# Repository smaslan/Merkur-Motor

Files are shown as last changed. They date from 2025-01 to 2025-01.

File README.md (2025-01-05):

# Stepper Motor Controller

This is simple project of one stepper motor controller designed for Czech toy 
[Merkur](https://www.merkurtoys.cz). It has manual speed and direction controlls and Bluetooth module for remote control via terminal commands or Android app. 
I don't expect this project as a whole would be useful to most people
but it may serve as a source for canibalization of some of its parts.

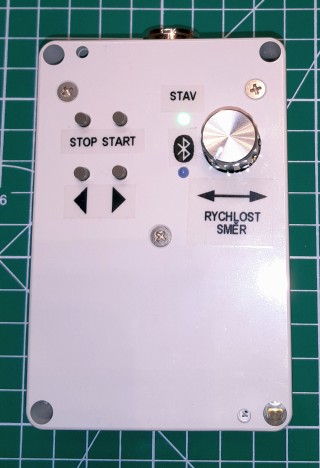
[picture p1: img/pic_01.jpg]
Controller box

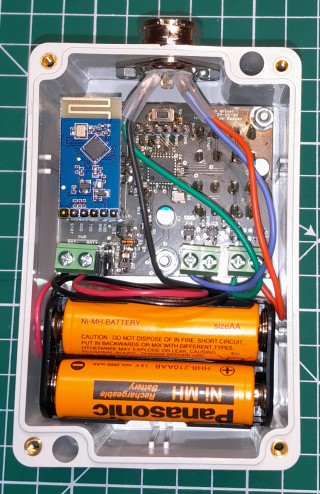
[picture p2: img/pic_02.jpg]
Controller insides


## Hardware

It was designed in a hurry from parts I had on hand so it's far from being optimal.
Core of the controller is 8-bit AVR [ATmega328PB](https://www.microchip.com/en-us/product/atmega328pb) (ATmega168PB would be enough). 
I used stepper motor [NEMA 17HS4023](https://www.google.com/search?q=NEMA+17+17HS4023) with bipolar coils.
I did not have proper stepper controller IC on hand, so I used cheap GaN fet driver ICs 
[1EDN7512B](https://www.infineon.com/cms/en/product/power/gate-driver-ics/1edn7512b/) with MOSFET half-bridge output.
These chips have undervoltage lockout (UVLO) circuit with threshold around 4.2V, which is kind of risky, because one of the bridge ICs will go to 
UVLO state before the other one, so there may be uninteruptable current via the winding when UVLO goes active. It won't be destructive, but it will discharge battery even faster, 
so UVLO is detected by AVR and it turns off power stage before it happens. Remote communication is made using cheap BT module
[JDY33-TTL](https://www.google.com/search?q=jdy33+ssp). Power stage, BT module and voltage sensing circuit can be switched off 
by power MOSFET to reduce idle power consumption to near zero (approx 2uA). Intended supply is from 4xAA NiMH accumulators, so there is 
5V voltage regulator for AVR. I used ultra-low quiscent current LDO TI [TPS709B50](https://www.ti.com/product/TPS709). 
Controlls are four buttons (Start, Stop, Left, Right) and encoder to setup speed.

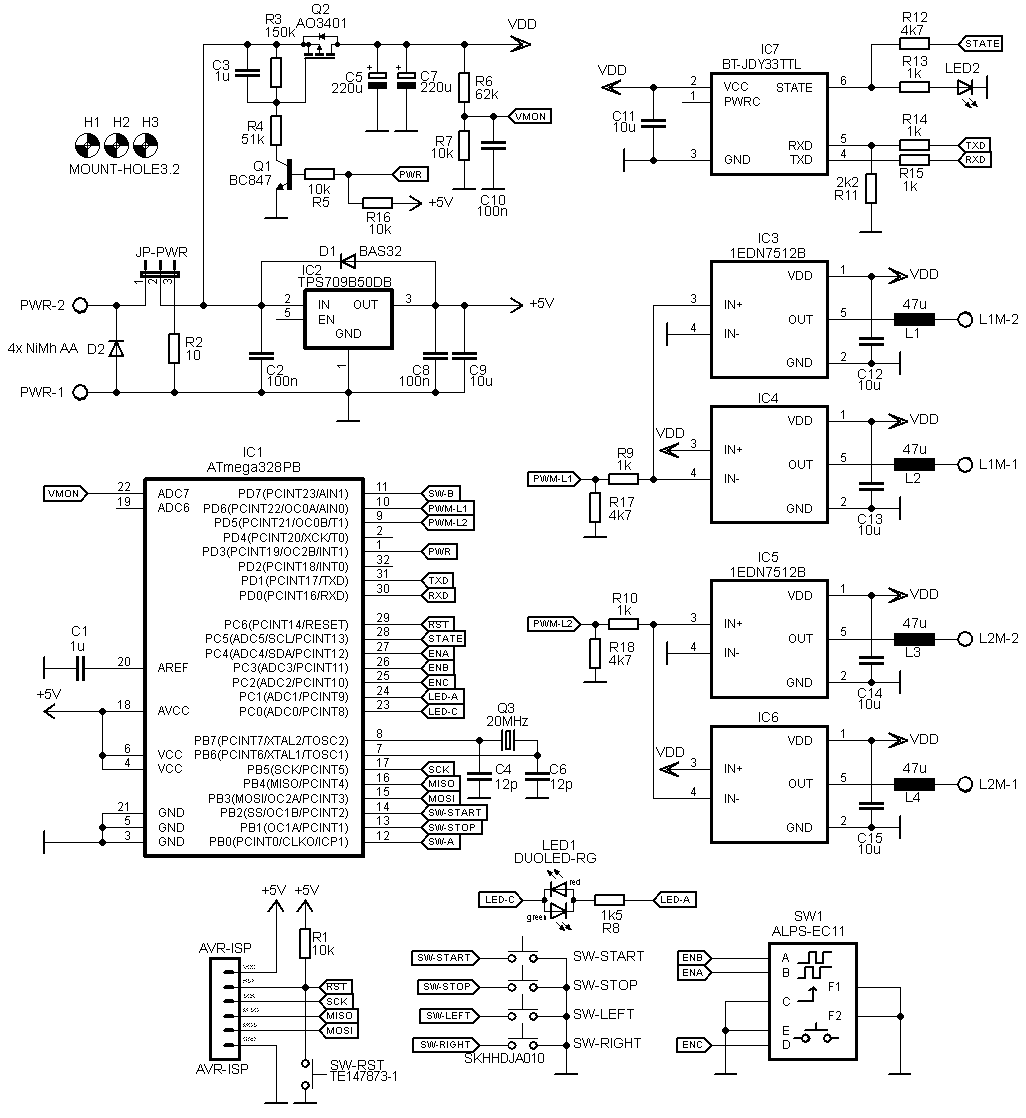
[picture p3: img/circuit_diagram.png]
Circuit diagram


The whole module was designed to fit in [plastic box](https://www.tme.eu/cz/details/km-276i_g/univerzalni-krabicky/maszczyk/). I wanted to make it smaller, but batteries are a bit large. Maybe in the next version. [PCB and diagram](./stepper_ctrl/) are available in Eagle format.

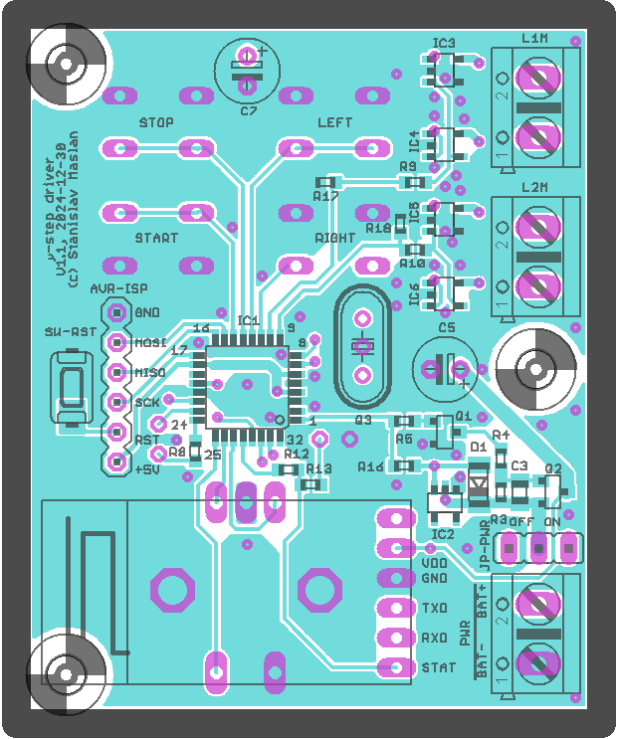
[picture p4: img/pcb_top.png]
PCB top layer

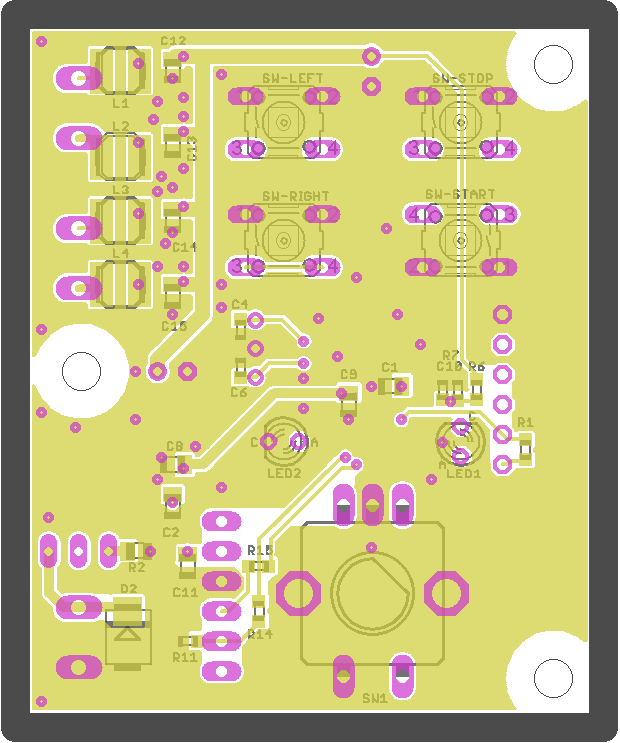
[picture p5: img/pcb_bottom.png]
PCB bottom layer


## AVR Firmware

Firmware for AVR is written in [Microchip Studio](https://www.microchip.com/en-us/tools-resources/develop/microchip-studio) using AVRGCC. 
Motor bridges are controlled by AVR PWM outputs which generate sine and cosine waves with modulation frequency of 78.125kHz, so it is kind of micro stepping driver. 
There is no current feedback from the stepper windings, so the current is controlled empirically by changing sine and consine amplitudes depending on motor speed. For the selected motor it should be approx 200 - 250mA with no load. Maximum speed is limited to 270rpm.
Reception of data via BT module is made in ISR to round buffer. Processing of the commands is done in main loop as well as controls state machine and other non-critical operations. Command interface uses simple [SCPI command](https://en.wikipedia.org/wiki/Standard_Commands_for_Programmable_Instruments) style commands set. Each command must be terminated by LF. Commands can be chained by semicolon. Answers are terminated by LF. Communication runs on BT module's default 9600bd. BT device name and its MAC address was left on default. List of supported commands:

```
 *IDN?                   - Return identification string.
 *OPC?                   - Wait for previous commands being processed, then returns 1.
 SYST:ERR?               - Return last error string.
 SYST:VMON?              - Return system voltage [V].
 SYST:TEMP?              - Return system temperature [degC].
 SYST:EESAVE             - Store current setup to EEPROM.
 SLEEP                   - Go to sleep mode immediately.
 SLEEP:TIMEOUT <timeout> - set sleep mode timeout [s].
 SLEEP:TIMEOUT?          - Get sleep timeout [s].
 SPEED <speed>           - Set motor speed in [rpm], signed value to set direction.
 SPEED?                  - Get current motor speed [rpm].
 SPEED:SET?              - Get last target (set) speed [rpm].
 SPEED:LIMIT <speed>     - Set speed limit [rpm].
 SPEED:LIMIT?            - Get speed limit [rpm].
 MOT:ACC <acc>           - Set motor acceleration constant [rpm/s].
 MOT:ACC?                - Get motor acceleration constant [rpm/s].
 START                   - Start motor to last set speed and direcion.
 STOP                    - Stop motor.
 DIR <direction>         - set motor direction (CW or CCW) 
                           and eventually start motor to previous speed.
```

Controller has implemented timeout timer, so when no controls are changed or SCPI command received, it will go to power down mode. It will respond to START button press to wakeup. It can be forced to power down mode by holding STOP button or by SCPI command SLEEP. Battery voltage is measured continuously. When it drops below preset threshold it will start blinking red and eventually turn off.

AVR fuse bits:
```
 Extended byte: CFD = 0, BODLEVEL[2..0] = 101 
 High byte: BOOTRST = 1, BOOTSZ[1..0] = 00, EESAVE = 0, WDTON = 1, SPIEN = 0, DWEN = 0, RSTDISBL = 1
 Low byte: CKSEL[3..0] = 1111, SUT[1..0] = 11, CKOUT = 1, CKDIV8 = 1
```

Firmware is available at [stepper_ctrl/fw_stepper_v1/](./stepper_ctrl/fw_stepper_v1).

## Android controll app "Merkur Motor"

Stepper controller can be controlled by terminal, but it's not exactly practical, so I decided to make an app for Android. This was my first atempt ever, so be warned it is not nice and optimal code but may be still used to cannibalize some parts. 
After some reading I decided to give a try to [Android Studio](https://developer.android.com/studio) and popular language [Kotlin](https://kotlinlang.org). That turned out to be good choice. Especially Kotlin is nice and simple language compared to e.g. C++. 
At first I tried to use some BT serial libraries, but I was not able to deal with collisions between some libraries so I tried to make BT communication using basic libraries. That was simpler than expected. Basically just list paired BT devices, select one, open BT socket and get in/out streams. Done. The worst part was dealing with permissions and trying to deal with loss of communication e.g. when the BT device goes offline. But in the end it kind of works at least from Android 11 to 14. Source is available at [MerkurControl/](./MerkurControl/).

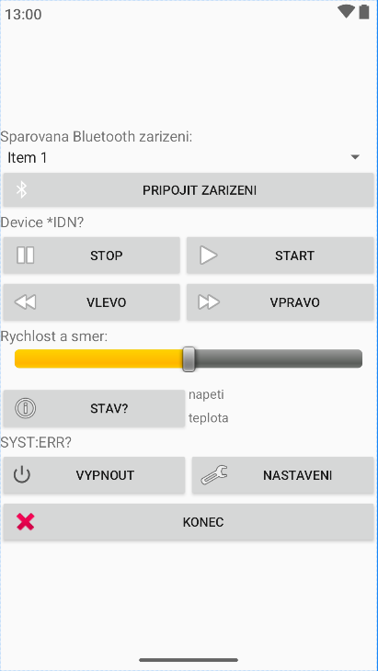
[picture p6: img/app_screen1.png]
Android app


## License
All parts of the project are distributed under [MIT license](./README.txt).

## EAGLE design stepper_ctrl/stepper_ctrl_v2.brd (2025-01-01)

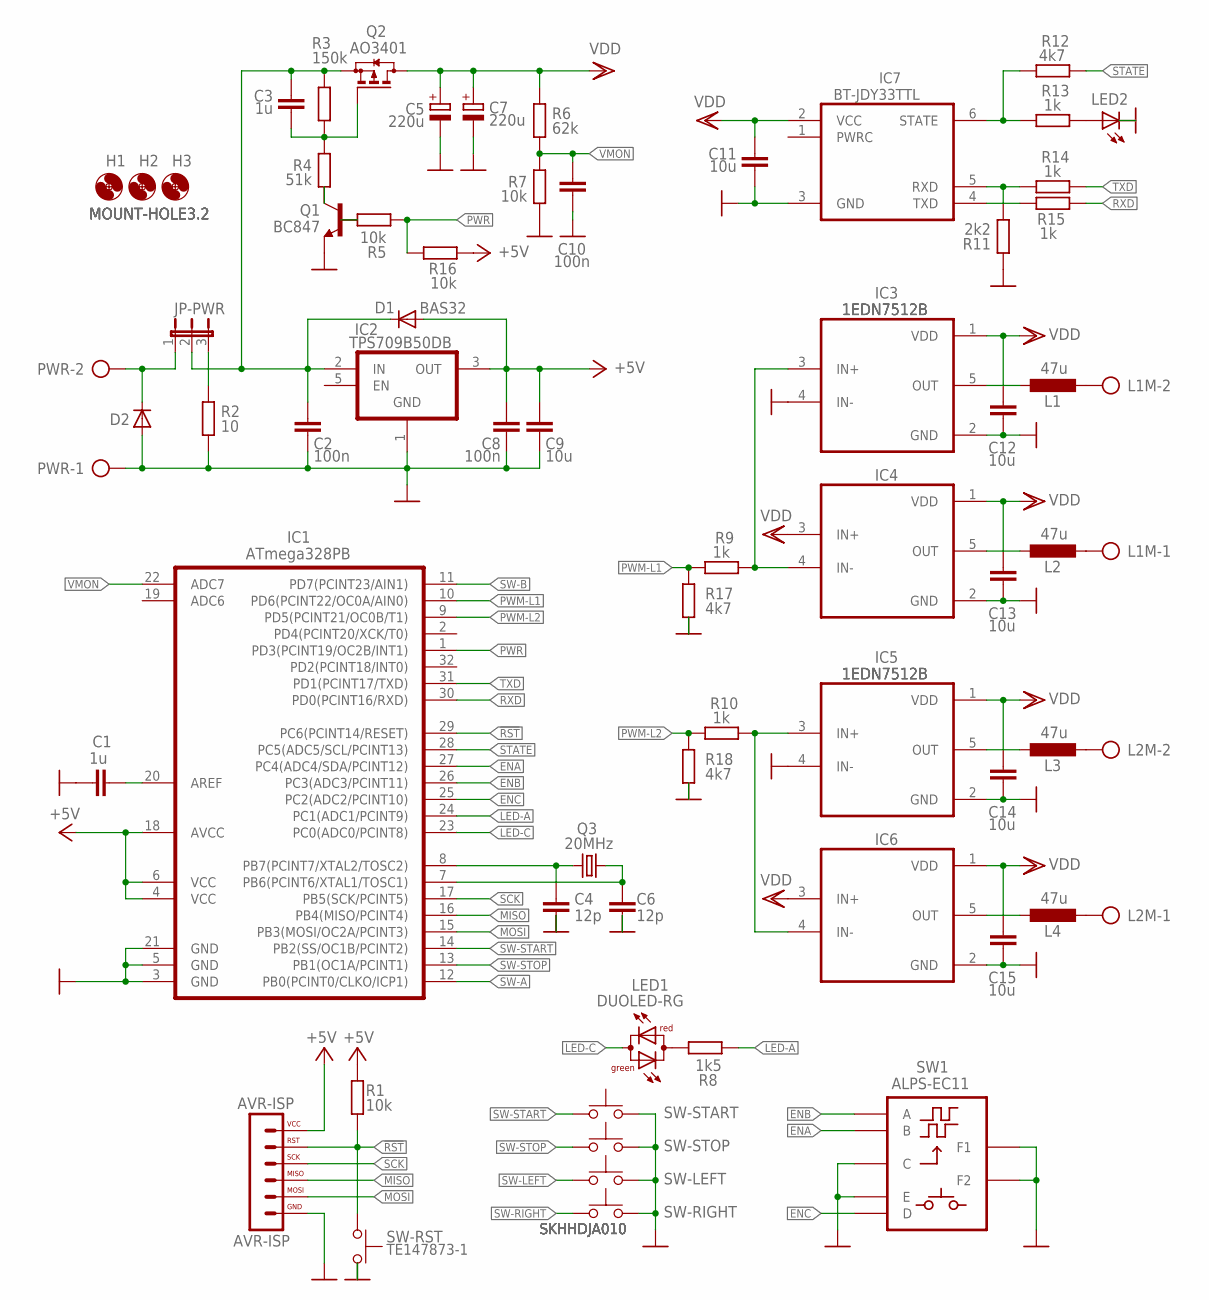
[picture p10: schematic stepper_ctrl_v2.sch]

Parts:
AVR-ISP: AVR-ISP; SIL6-NNRND
C1, C3: 1u; C0805K
C2, C8: 100n; C0805K
C4, C6: 12p; C0603K
C5, C7: 220u; E2,5-6
C9, C11, C12, C13, C14, C15: 10u; C0805K
C10: 100n; C0603K
D1: BAS32; SOD80C
D2: DIODE-SMB; SMB
H1, H2, H3: MOUNT-HOLE3.2; 3,2
IC1: ATmega328PB; TQFP32
IC2: TPS709B50DB; SOT23-5
IC3, IC4, IC5, IC6: 1EDN7512B; SOT23-5
IC7: BT-JDY33TTL; BT-JFY33TTL
JP-PWR: JP2EB; JP2YB
L1, L2, L3, L4: 47u; L4018
L1M, L2M: AK500/2
LED1: DUOLED-RG; LED3MM
LED2: LED3MM
PWR: AK500/2
Q1: BC847; SOT23
Q2: AO3401; SOT23
Q3: 20MHz; HC49U-V
R1, R5, R7, R16: 10k; R0603
R2: 10; R0805
R3: 150k; R0603
R4: 51k; R0603
R6: 62k; R0603
R8: 1k5; R0603
R9, R10, R13, R14, R15: 1k; R0603
R11: 2k2; R0603
R12, R17, R18: 4k7; R0603
SW1: ALPS-EC11; ALPS_EC11
SW-LEFT: SKHHDJA010; CUDL1
SW-RIGHT: SKHHDJA010; CUDL1
SW-RST: TE147873-1; TE-147873-1
SW-START: SKHHDJA010; CUDL1
SW-STOP: SKHHDJA010; CUDL1

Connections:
!RST: AVR-ISP.5, IC1.29 (PC6(PCINT14/RESET)), R1.2, SW-RST.P$2
+5V: AVR-ISP.6, C8.1, C9.1, D1.A, IC1.4 (VCC), IC1.6 (VCC), IC1.18 (AVCC), IC2.3 (OUT), R1.1, R16.2
ENA: IC1.27 (PC4(ADC4/SDA/PCINT12)), SW1.B
ENB: IC1.26 (PC3(ADC3/PCINT11)), SW1.A
ENC: IC1.25 (PC2(ADC2/PCINT10)), SW1.D
GND: AVR-ISP.1, C1.1, C2.2, C4.2, C5.-, C6.2, C7.-, C8.2, C9.2, C10.2, C11.2, C12.2, C13.2, C14.2, C15.2, D2.A, IC1.3 (GND), IC1.5 (GND), IC1.21 (GND), IC2.1 (GND), IC3.2 (GND), IC3.4 (IN-), IC4.2 (GND), IC5.2 (GND), IC5.4 (IN-), IC6.2 (GND), IC7.3 (GND), LED2.K (C), PWR.1, Q1.2 (E), R2.1, R7.1, R11.2, R17.2, R18.2, SW1.C, SW1.E, SW1.F1, SW1.F2, SW-LEFT.1, SW-LEFT.2, SW-RIGHT.1, SW-RIGHT.2, SW-RST.P$1, SW-START.1, SW-START.2, SW-STOP.1, SW-STOP.2
LED-A: IC1.24 (PC1(ADC1/PCINT9)), R8.1
LED-C: IC1.23 (PC0(ADC0/PCINT8)), LED1.K (C)
MISO: AVR-ISP.3, IC1.16 (PB4(MISO/PCINT4))
MOSI: AVR-ISP.2, IC1.15 (PB3(MOSI/OC2A/PCINT3))
unnamed: IC3.3 (IN+), IC4.4 (IN-), R9.1
unnamed: C1.2, IC1.20 (AREF)
unnamed: C2.1, C3.1, D1.C, IC2.2 (IN), JP-PWR.2, Q2.2 (S), R3.1
unnamed: D2.C, JP-PWR.1, PWR.2
unnamed: IC5.3 (IN+), IC6.4 (IN-), R10.1
unnamed: JP-PWR.3, R2.2
unnamed: LED2.A, R13.1
unnamed: IC7.6 (STATE), R12.2, R13.2
unnamed: IC7.5 (RXD), R11.1, R14.2
unnamed: IC7.4 (TXD), R15.2
unnamed: C4.1, IC1.8 (PB7(PCINT7/XTAL2/TOSC2)), Q3.1
unnamed: C6.1, IC1.7 (PB6(PCINT6/XTAL1/TOSC1)), Q3.2
unnamed: Q1.1 (B), R5.2
unnamed: LED1.A, R8.2
unnamed: IC3.5 (OUT), L1.2
unnamed: IC4.5 (OUT), L2.2
unnamed: IC5.5 (OUT), L3.2
unnamed: IC6.5 (OUT), L4.2
unnamed: L1.1, L1M.2
unnamed: L2M.2, L3.1
unnamed: L2M.1, L4.1
unnamed: L1M.1, L2.1
unnamed: C3.2, Q2.1 (G), R3.2, R4.2
unnamed: Q1.3 (C), R4.1
PWM-L1: IC1.10 (PD6(PCINT22/OC0A/AIN0)), R9.2, R17.1
PWM-L2: IC1.9 (PD5(PCINT21/OC0B/T1)), R10.2, R18.1
PWR: IC1.1 (PD3(PCINT19/OC2B/INT1)), R5.1, R16.1
RXD: IC1.30 (PD0(PCINT16/RXD)), R15.1
SCK: AVR-ISP.4, IC1.17 (PB5(SCK/PCINT5))
STATE: IC1.28 (PC5(ADC5/SCL/PCINT13)), R12.1
SW-A: IC1.12 (PB0(PCINT0/CLKO/ICP1))
SW-B: IC1.11 (PD7(PCINT23/AIN1))
SW-LEFT: SW-LEFT.3, SW-LEFT.4
SW-RIGHT: SW-RIGHT.3, SW-RIGHT.4
SW-START: IC1.14 (PB2(SS/OC1B/PCINT2)), SW-START.3, SW-START.4
SW-STOP: IC1.13 (PB1(OC1A/PCINT1)), SW-STOP.3, SW-STOP.4
TXD: IC1.31 (PD1(PCINT17/TXD)), R14.1
VDD: C5.+, C7.+, C11.1, C12.1, C13.1, C14.1, C15.1, IC3.1 (VDD), IC4.1 (VDD), IC4.3 (IN+), IC5.1 (VDD), IC6.1 (VDD), IC6.3 (IN+), IC7.2 (VCC), Q2.3 (D), R6.2
VMON: C10.1, IC1.22 (ADC7), R6.1, R7.2

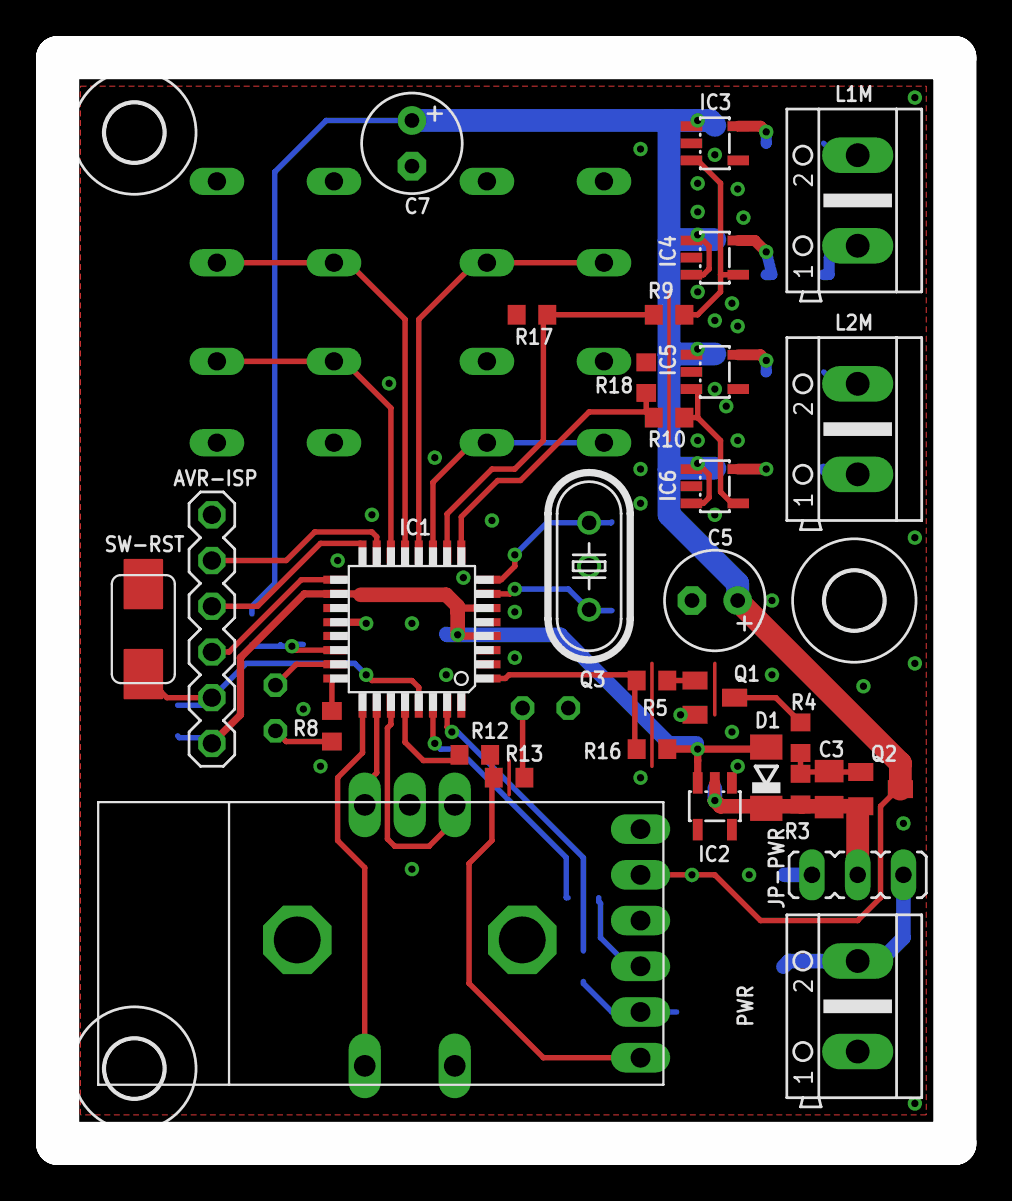
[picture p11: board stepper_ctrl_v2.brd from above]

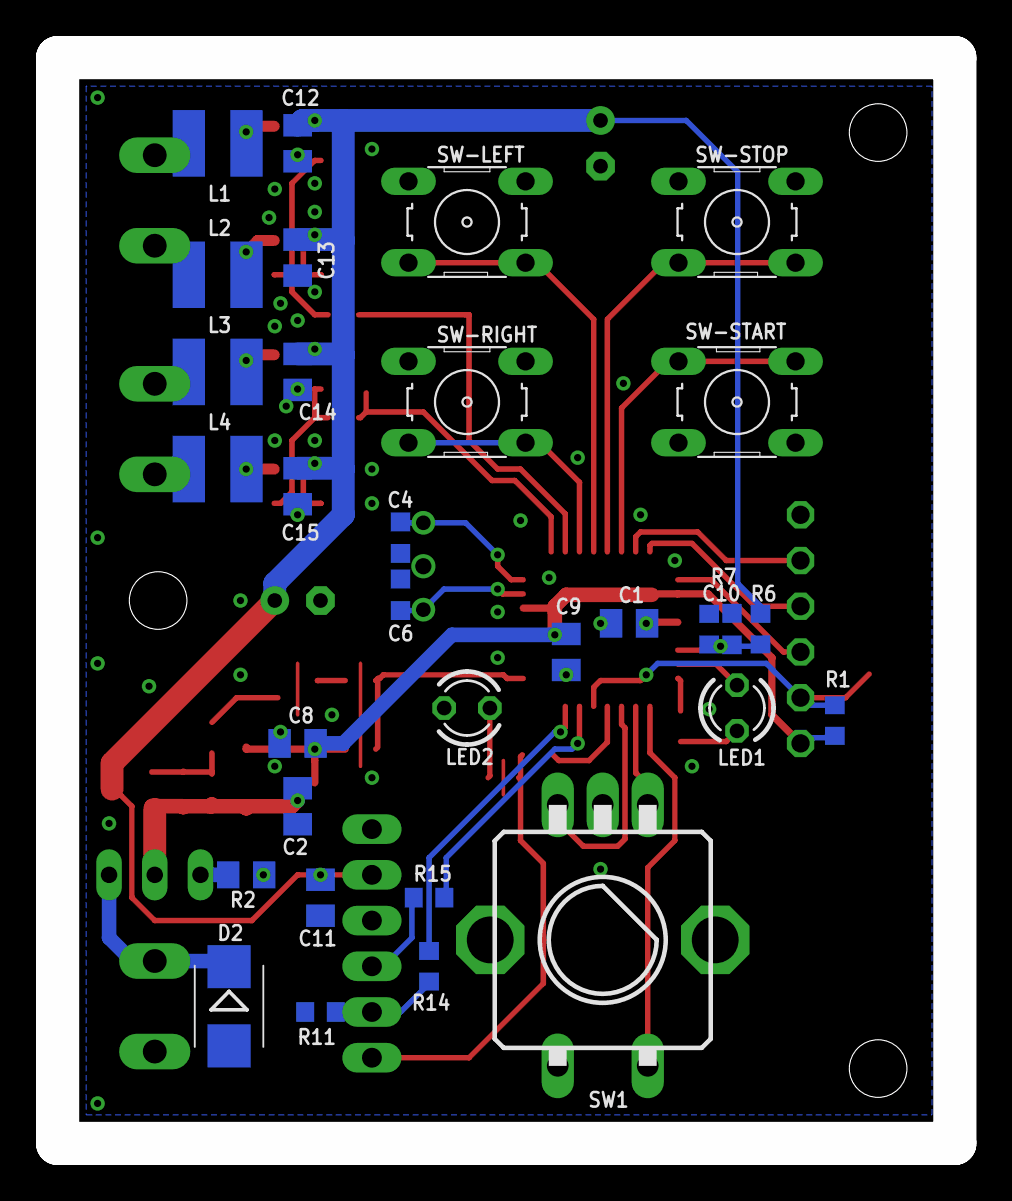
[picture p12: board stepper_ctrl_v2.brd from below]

Board: 2 copper layers, 49.8 x 60.3 mm, 65 parts (31 on the bottom side), 47 nets.

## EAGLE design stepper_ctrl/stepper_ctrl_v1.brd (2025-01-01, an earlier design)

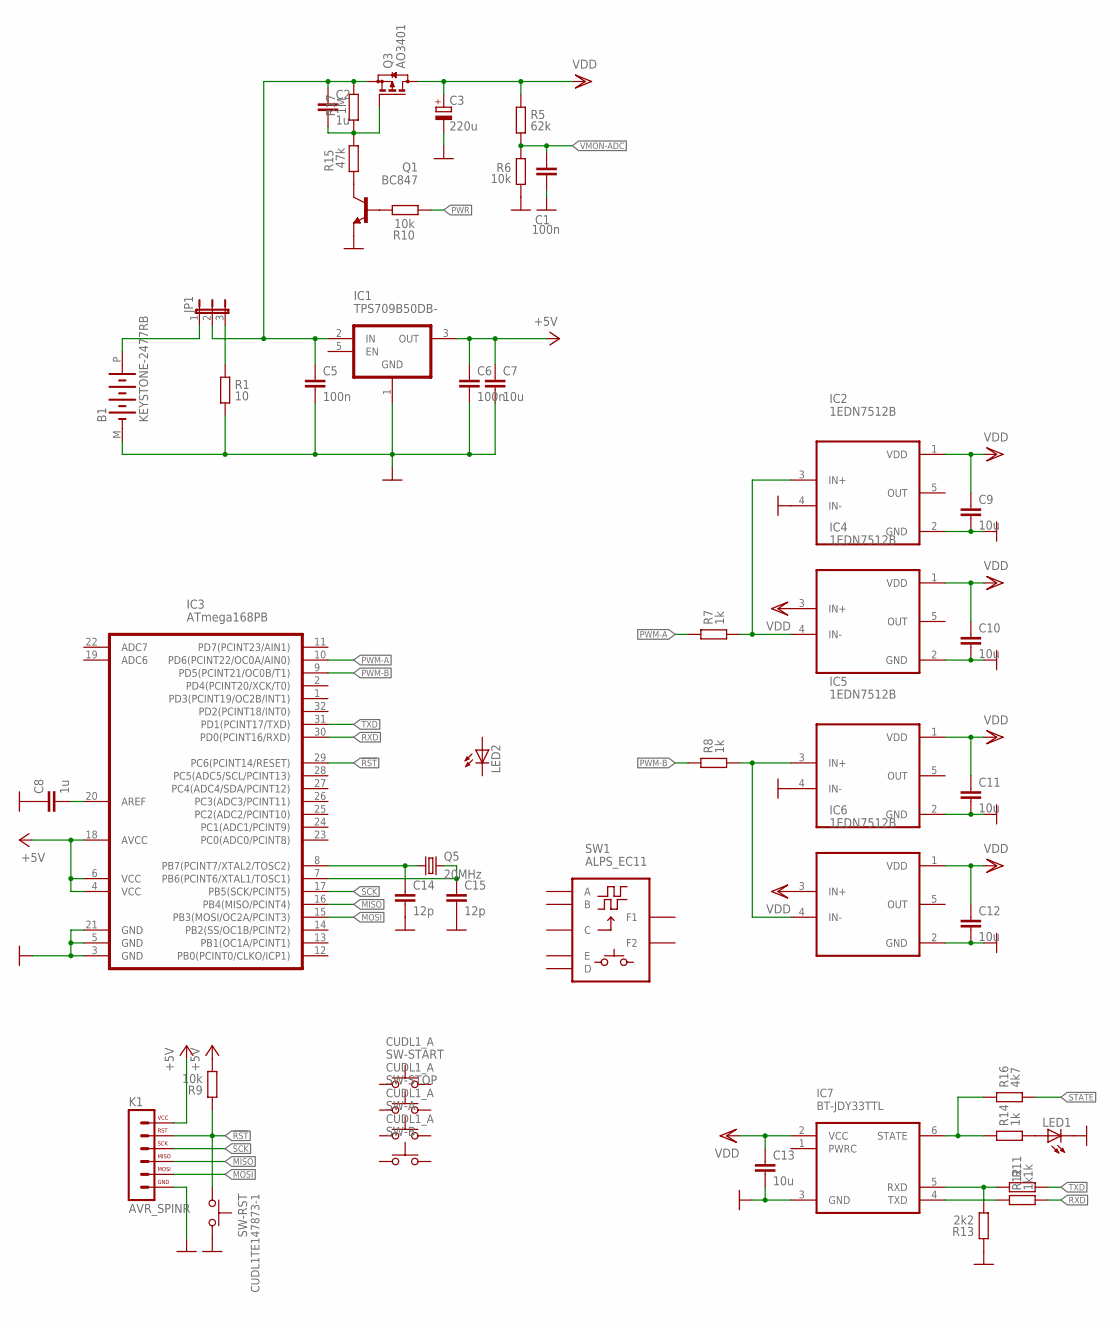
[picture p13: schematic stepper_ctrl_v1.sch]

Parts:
B1: KEYSTONE-2477RB
C1: 100n; C0603K
C2, C8: 1u; C0805K
C3: 220u; E2,5-7
C5, C6: 100n; C0805K
C7, C9, C10, C11, C12, C13: 10u; C0805K
C14, C15: 12p; C0603K
IC1: TPS709B50DB-; SOT23-5
IC2, IC4, IC5, IC6: 1EDN7512B; SOT23-5
IC3: ATmega168PB; TQFP32
IC7: BT-JDY33TTL; BT-JFY33TTL
JP1: JP2EB; JP2YB
K1: AVR_SPINR; SIL6-NNRND
LED1, LED2: LED3MM
Q1: BC847; SOT23
Q3: AO3401; SOT23
Q5: 20MHz; SMD32X25
R1: 10; R0805
R5: 62k; R0603
R6, R9, R10: 10k; R0603
R7, R8, R11, R12, R14: 1k; R0603
R13: 2k2; R0603
R15: 47k; R0603
R16: 4k7; R0603
R17: 1M; R0603
SW1: ALPS_EC11
SW-A: CUDL1_A; CUDL1
SW-B: CUDL1_A; CUDL1
SW-RST: CUDL1TE147873-1; TE-147873-1
SW-START: CUDL1_A; CUDL1
SW-STOP: CUDL1_A; CUDL1

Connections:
!RST: IC3.29 (PC6(PCINT14/RESET)), K1.5, R9.2, SW-RST.P$2
+5V: C6.1, C7.1, IC1.3 (OUT), IC3.4 (VCC), IC3.6 (VCC), IC3.18 (AVCC), K1.6, R9.1
GND: B1.M (-), C1.2, C3.-, C5.2, C6.2, C7.2, C8.1, C9.2, C10.2, C11.2, C12.2, C13.2, C14.2, C15.2, IC1.1 (GND), IC2.2 (GND), IC2.4 (IN-), IC3.3 (GND), IC3.5 (GND), IC3.21 (GND), IC4.2 (GND), IC5.2 (GND), IC5.4 (IN-), IC6.2 (GND), IC7.3 (GND), K1.1, LED1.K (C), Q1.2 (E), R1.1, R6.1, R13.2, SW-RST.P$1
MISO: IC3.16 (PB4(MISO/PCINT4)), K1.3
MOSI: IC3.15 (PB3(MOSI/OC2A/PCINT3)), K1.2
unnamed: IC2.3 (IN+), IC4.4 (IN-), R7.1
unnamed: C8.2, IC3.20 (AREF)
unnamed: C2.1, C5.1, IC1.2 (IN), JP1.2, Q3.2 (S), R17.1
unnamed: B1.P (+), JP1.1
unnamed: IC5.3 (IN+), IC6.4 (IN-), R8.1
unnamed: JP1.3, R1.2
unnamed: LED1.A, R14.1
unnamed: IC7.6 (STATE), R14.2, R16.2
unnamed: IC7.5 (RXD), R11.2, R13.1
unnamed: IC7.4 (TXD), R12.2
unnamed: C14.1, IC3.8 (PB7(PCINT7/XTAL2/TOSC2)), Q5.1
unnamed: C15.1, IC3.7 (PB6(PCINT6/XTAL1/TOSC1)), Q5.3 (2)
unnamed: Q1.1 (B), R10.2
unnamed: C2.2, Q3.1 (G), R15.2, R17.2
unnamed: Q1.3 (C), R15.1
PWM-A: IC3.10 (PD6(PCINT22/OC0A/AIN0)), R7.2
PWM-B: IC3.9 (PD5(PCINT21/OC0B/T1)), R8.2
PWR: R10.1
RXD: IC3.30 (PD0(PCINT16/RXD)), R12.1
SCK: IC3.17 (PB5(SCK/PCINT5)), K1.4
STATE: R16.1
TXD: IC3.31 (PD1(PCINT17/TXD)), R11.1
VDD: C3.+, C9.1, C10.1, C11.1, C12.1, C13.1, IC2.1 (VDD), IC4.1 (VDD), IC4.3 (IN+), IC5.1 (VDD), IC6.1 (VDD), IC6.3 (IN+), IC7.2 (VCC), Q3.3 (D), R5.2
VMON-ADC: C1.1, R5.1, R6.2

Board: 2 copper layers, 49 parts (36 on the bottom side), 27 nets, no tracks yet.

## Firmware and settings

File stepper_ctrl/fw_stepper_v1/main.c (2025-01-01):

/*
 * Simple stepper motor controller. More details here:
 * https://github.com/smaslan/Merkur-Motor
 *
 * (c) 2024-2025, Stanislav Maslan, s.maslan@seznam.cz
 * V1.0, 2025-01-01
 *
 * The code and all its part are distributed under MIT license
 * https://opensource.org/licenses/MIT.
 */ 

#include <avr/io.h>
#include <avr/sleep.h>
#include <avr/pgmspace.h>
#include <avr/interrupt.h>
#include <avr/wdt.h>
#include <avr/boot.h>
#include <avr/sfr_defs.h>
#include <util/atomic.h>
#include <util/delay_basic.h>
#include <util/delay.h>
#include <string.h>
#include <stdio.h>
#include <stdlib.h>

#include "main.h"
#include "serial.h"

// --- jump to address ---
#define boot_start(boot_addr) {goto *(const void*)boot_addr;}



//----------------------------------------------------------------------------------
// analog ADC stuff
//----------------------------------------------------------------------------------

TADC adc_data;

#define ADC_VREF 1.1f
#define ADC_VMON_DIV (10000.0/(10000.0 + 62000.0))
#define ADC_GAIN (ADC_VREF/(ADC_AVG*1024.0f))
#define ADC_VMON_CAL (ADC_GAIN/ADC_VMON_DIV)


// ADC conversion done (polling mode)
//ISR(ADC_vect)
uint8_t adc_conv_done()
{
	//sei();
	if(!bit_is_set(ADCSRA,ADIF))
		return(0);

	// average buffer
	static uint8_t avg_cnt = ADC_AVG;
	uint8_t chn = (ADMUX >> MUX0)&0x0F;
	
	static uint16_t temp = 0;
	static uint16_t vmon = 0;
		
	if(chn == ADC_VMON_MUX)
	{
		// VMON measured
		vmon += ADC;		
		chn = ADC_TEMP_MUX;
	}
	else if(chn == ADC_TEMP_MUX)
	{
		// temperature measured
		temp += ADC;
		chn	= ADC_VMON_MUX;
	}

	avg_cnt--;
	if(!avg_cnt)
	{
		avg_cnt = ADC_AVG;
		if(chn == ADC_VMON_MUX)
		{
			adc_data.a_vmon = vmon; vmon = 0;
			adc_data.a_temp = temp; temp = 0;
		}

		// next channel
		ADMUX = (ADMUX & ~(0x0F<<MUX0)) | (chn<<MUX0);
	}
	
	// start next conversion
	sbi(ADCSRA,ADIF);
	sbi(ADCSRA,ADSC);
	
	return(1);
}

// get VMON voltage [V]
float adc_get_vmon()
{
	uint16_t a_vmon = 0;
	//ATOMIC_BLOCK(ATOMIC_RESTORESTATE)
	{
		a_vmon = adc_data.a_vmon;
	}
	return(ADC_VMON_CAL*a_vmon);
}

// set Vmon low limit allert
void adc_set_vmon_alert(float vmin_min)
{
	adc_data.vmon_alert = vmin_min/ADC_VMON_CAL;
}

// check Vmon alert
uint8_t adc_check_vmon()
{
	uint16_t a_vmon = 0;
	//ATOMIC_BLOCK(ATOMIC_RESTORESTATE)
	{
		a_vmon = adc_data.a_vmon;
	}
	if(!isnan(adc_data.vmon_alert) && a_vmon < adc_data.vmon_alert)
		return(1);
	return(0);
}

// get temperature [degC]
float adc_get_temp()
{	
	uint16_t a_temp = 0; 
	//ATOMIC_BLOCK(ATOMIC_RESTORESTATE)
	{
		a_temp = adc_data.a_temp;
	}		
	return((float)(a_temp/ADC_AVG) - 280.0);
}

// init ADC
void adc_init()
{
	// initial ADC setup (AVcc ref)
	ADMUX = (3<<REFS0)|(0<<ADLAR)|(ADC_VMON_MUX<<MUX0);
	ADCSRA = (1<<ADEN)|(0<<ADATE)|(0<<ADIE)|(7<<ADPS0);
	ADCSRB = (0<<ADTS0);
	
	// start ADC conversion loop
	sbi(ADCSRA,ADSC);
	
	// initial measured value
	adc_data.a_vmon = 0;
	adc_data.a_temp = 0;

	// set default vmon alert
	adc_set_vmon_alert(NAN);
}

// idle ADC before sleep
void adc_idle()
{
	ADCSRA = 0;
}

//----------------------------------------------------------------------------------
// PWM controllers
//----------------------------------------------------------------------------------

typedef struct{
	uint16_t phi;
	int16_t step;
	uint8_t amp;
}TPWM;
TPWM pwm;

void pwm_init()
{
	// fast PWM
	TCCR0A = (2<<COM0A0)|(2<<COM0B0)|(3<<WGM00);
	TCCR0B = (0<<WGM02)|(1<<CS00);
	TIMSK0 = (1<<TOIE0);

	// default duty
	OCR0A = 127;
	OCR0B = 127;

	// PWM outputs
	sbi(PWM_ddr, PWM_L1);
	sbi(PWM_ddr, PWM_L2);

	// power stage control
	cbi(PWR_ddr, PWR);
	cbi(PWR_port, PWR);

	pwm.amp = 0;
	pwm.phi = 0;
	pwm.step = 0;
}

// start PWM generation
void pwm_enable()
{
	TCCR0A = (2<<COM0A0)|(2<<COM0B0)|(3<<WGM00);
	sbi(PWR_port, PWR);
}


// idle PWM generation (sets zero current), disable power
void pwm_idle()
{
	pwm.amp = 0;
	cbi(PWR_port, PWR);
}

// start PWM generation
void pwm_disable()
{
	TCCR0A = (0<<COM0A0)|(0<<COM0B0)|(0<<WGM00);
	cbi(PWM_port, PWM_L1);
	cbi(PWM_port, PWM_L2);	
}



// PWM wrap-around ISR
ISR(TIMER0_OVF_vect)
{
	// sin(), cos() LUT
	static const int8_t sico[] PROGMEM = {
		0, 127,   3, 127,   6, 127,   9, 127,  12, 126,  16, 126,  19, 126,  22, 125,
		25, 125,  28, 124,  31, 123,  34, 122,  37, 122,  40, 121,  43, 120,  46, 118,
		49, 117,  51, 116,  54, 115,  57, 113,  60, 112,  63, 111,  65, 109,  68, 107,
		71, 106,  73, 104,  76, 102,  78, 100,  81,  98,  83,  96,  85,  94,  88,  92,
		90,  90,  92,  88,  94,  85,  96,  83,  98,  81, 100,  78, 102,  76, 104,  73,
		106,  71, 107,  68, 109,  65, 111,  63, 112,  60, 113,  57, 115,  54, 116,  51,
		117,  49, 118,  46, 120,  43, 121,  40, 122,  37, 122,  34, 123,  31, 124,  28,
		125,  25, 125,  22, 126,  19, 126,  16, 126,  12, 127,   9, 127,   6, 127,   3,
		127,   0, 127,  -3, 127,  -6, 127,  -9, 126, -12, 126, -16, 126, -19, 125, -22,
		125, -25, 124, -28, 123, -31, 122, -34, 122, -37, 121, -40, 120, -43, 118, -46,
		117, -49, 116, -51, 115, -54, 113, -57, 112, -60, 111, -63, 109, -65, 107, -68,
		106, -71, 104, -73, 102, -76, 100, -78,  98, -81,  96, -83,  94, -85,  92, -88,
		90, -90,  88, -92,  85, -94,  83, -96,  81, -98,  78,-100,  76,-102,  73,-104,
		71,-106,  68,-107,  65,-109,  63,-111,  60,-112,  57,-113,  54,-115,  51,-116,
		49,-117,  46,-118,  43,-120,  40,-121,  37,-122,  34,-122,  31,-123,  28,-124,
		25,-125,  22,-125,  19,-126,  16,-126,  12,-126,   9,-127,   6,-127,   3,-127,
		0,-127,  -3,-127,  -6,-127,  -9,-127, -12,-126, -16,-126, -19,-126, -22,-125,
		-25,-125, -28,-124, -31,-123, -34,-122, -37,-122, -40,-121, -43,-120, -46,-118,
		-49,-117, -51,-116, -54,-115, -57,-113, -60,-112, -63,-111, -65,-109, -68,-107,
		-71,-106, -73,-104, -76,-102, -78,-100, -81, -98, -83, -96, -85, -94, -88, -92,
		-90, -90, -92, -88, -94, -85, -96, -83, -98, -81,-100, -78,-102, -76,-104, -73,
		-106, -71,-107, -68,-109, -65,-111, -63,-112, -60,-113, -57,-115, -54,-116, -51,
		-117, -49,-118, -46,-120, -43,-121, -40,-122, -37,-122, -34,-123, -31,-124, -28,
		-125, -25,-125, -22,-126, -19,-126, -16,-126, -12,-127,  -9,-127,  -6,-127,  -3,
		-127,   0,-127,   3,-127,   6,-127,   9,-126,  12,-126,  16,-126,  19,-125,  22,
		-125,  25,-124,  28,-123,  31,-122,  34,-122,  37,-121,  40,-120,  43,-118,  46,
		-117,  49,-116,  51,-115,  54,-113,  57,-112,  60,-111,  63,-109,  65,-107,  68,
		-106,  71,-104,  73,-102,  76,-100,  78, -98,  81, -96,  83, -94,  85, -92,  88,
		-90,  90, -88,  92, -85,  94, -83,  96, -81,  98, -78, 100, -76, 102, -73, 104,
		-71, 106, -68, 107, -65, 109, -63, 111, -60, 112, -57, 113, -54, 115, -51, 116,
		-49, 117, -46, 118, -43, 120, -40, 121, -37, 122, -34, 122, -31, 123, -28, 124,
		-25, 125, -22, 125, -19, 126, -16, 126, -12, 126,  -9, 127,  -6, 127,  -3, 127};
	
	uint16_t phi = pwm.phi;
	phi += pwm.step;
	pwm.phi = phi;

	int8_t const *p = &sico[2*(uint16_t)(phi >> 8)];

	int8_t isin = pgm_read_byte(p++);
	int8_t icos = pgm_read_byte(p++);

	uint8_t amp = pwm.amp;
	OCR0A = 128 + ((isin*amp)>>8);
	OCR0B = 128 + ((icos*amp)>>8);
}

// update motor calibration coefs (call when motor parameters are changed)
void mot_update_cal(TMotor *mot)
{
	mot->amp_coef = (mot->amp_max - mot->amp_min)/(mot->speed_max - mot->speed_min);
}

// calc motor amplitude based on speed and cal data
uint8_t mot_get_amp(TMotor *mot, float speed)
{
	float amp = (fabs(speed) - mot->speed_min)*mot->amp_coef + mot->amp_min;
	if(amp < mot->amp_min)
	amp = mot->amp_min;
	else if(amp > mot->amp_max)
	amp = mot->amp_max;
	return((uint8_t)amp);
}




//----------------------------------------------------------------------------------
// system timer
//----------------------------------------------------------------------------------

// init controls
void ctrl_init()
{
	// init encoder
	cbi(ENC_ddr, ENC_phy);
	cbi(ENC_ddr, ENA_phy);
	cbi(ENC_ddr, ENB_phy);
	sbi(ENC_port, ENC_phy);
	sbi(ENC_port, ENA_phy);
	sbi(ENC_port, ENB_phy);

	// init buttons
	cbi(SW_A_ddr, SW_A);
	cbi(SW_B_ddr, SW_B);
	cbi(SW_START_ddr, SW_START);
	cbi(SW_STOP_ddr, SW_STOP);
	sbi(SW_A_port, SW_A);
	sbi(SW_B_port, SW_B);
	sbi(SW_START_port, SW_START);
	sbi(SW_STOP_port, SW_STOP);

	// enable pin change ISRs for sleep wakeup
	PCICR = (1<<SW_START_PCIE)|(1<<ENC_PCIE);
	SW_START_PCMSK_REG |= SW_START_PCMSK;
	ENC_PCMSK_REG |= ENC_PCMSK;
}

// controls to idle (for low power)
void ctrl_idle()
{
	// idle encoder
	//cbi(ENC_port, ENC_phy);
	cbi(ENC_port, ENA_phy);
	cbi(ENC_port, ENB_phy);

	// idle buttons
	/*cbi(SW_A_port, SW_A);
	cbi(SW_B_port, SW_B);
	cbi(SW_START_port, SW_START);
	cbi(SW_STOP_port, SW_STOP);*/
}

// pin change stub ISRs
ISR(ENC_ISR)
{
}
ISR(SW_START_ISR)
{
}



// state LED mode
volatile uint8_t led_state;

// init state LED
void led_init()
{
	sbi(LED_ddr, LED_A);
	sbi(LED_ddr, LED_C);
	cbi(LED_port, LED_A);
	cbi(LED_port, LED_C);
	led_state = LED_IDLE;
}

// set state LED state
void led_set(uint8_t state)
{
	if(state == LED_IDLE)
	{
		cbi(LED_port, LED_A);
		cbi(LED_port, LED_C);
	}
	else if(state == LED_RED)
	{
		cbi(LED_port, LED_A);
		sbi(LED_port, LED_C);
	}
	else if(state == LED_GREEN)
	{
		sbi(LED_port, LED_A);
		cbi(LED_port, LED_C);
	}
}

// controls flags
TUI ui;

// process rotary encode sample
void re_sample(uint8_t states, uint8_t ups)
{
	// interval timer (~1ms resolution)
	static uint8_t timer = 0;
	if(timer<0xFFu)
	timer++;
	
	if(bit_is_set(ups, ENA))
	{
		// increment size
		int8_t s = max(max(50 - timer,1)>>2,1);
		
		// reset pulse interval timer
		timer = 0;

		// update value
		ui.enc_delta += (bit_is_set(states,ENB))?-s:+s;
		ui.flags |= (1<<UI_ENC_CHANGE);
	}
}

// LED timeout timer
volatile uint8_t timeout_led;
void set_led_timeout(uint8_t time)
{
	timeout_led = time;
}
uint8_t check_led_timeout(void)
{
	return(!timeout_led);
}

// uvlo timeout
volatile uint8_t uvlo_timeout;
void set_uvlo_timeout(uint8_t time)
{
	uvlo_timeout = time;
}
uint8_t check_uvlo_timeout(void)
{
	return(!uvlo_timeout);
}

// sleep timeout timer
volatile uint16_t timeout_sleep;
void set_sleep_timeout(uint16_t time)
{
	ATOMIC_BLOCK(ATOMIC_FORCEON)
	{
		timeout_sleep = time;
	}
}
// get sleep timout residual time
uint16_t get_sleep_timeout()
{
	uint16_t time = 0;
	ATOMIC_BLOCK(ATOMIC_FORCEON)
	{
		time = timeout_sleep;
	}
	return(time);
}
// check if sleep timeout done
uint8_t check_sleep_timeout()
{
	uint16_t time = 0;
	ATOMIC_BLOCK(ATOMIC_FORCEON)
	{
		time = timeout_sleep;
	}
	return(time == 0);
}

// system flags
volatile uint8_t sys_flags;

// system tick
ISR(TIMER1_COMPA_vect, ISR_NOBLOCK)
{
	//sei();

	// control states
	uint8_t states = 0x00;
	bcopy(states, SW_A, SW_A_pin, SW_A);
	bcopy(states, SW_B, SW_B_pin, SW_B);
	bcopy(states, SW_START, SW_START_pin, SW_START);
	bcopy(states, SW_STOP, SW_STOP_pin, SW_STOP);
	bcopy(states, ENC, ENC_pin, ENC_phy);
	bcopy(states, ENA, ENC_pin, ENA_phy);
	bcopy(states, ENB, ENC_pin, ENB_phy);
	
	// detect UI changes
	static uint8_t states_last = 0;
	uint8_t edges = states^states_last;
	ui.downs |= edges&(~states);
	uint8_t ups = edges&states;
	ui.states = ~states;
	states_last = states;

	// process encoder rotation
	re_sample(states, ups);

	static uint8_t led_blink = 0;
	static uint8_t tick_blink_div = 0;
	static uint8_t tick_10ms_div = 0;
	static uint8_t tick_1s_div = 0;
	static uint8_t hold_dly[8] = {0,0,0,0,0,0,0,0};
	tick_10ms_div--;
	if(!tick_10ms_div)
	{
		// 10ms tick
		tick_10ms_div = 10;
		sys_flags |= 1<<SYS_10MS_TICK;

		// detect button holdoffs
		uint8_t stats = ~states;
		uint8_t holds = 0;
		for(uint8_t k = 0; k < 8; k++)
		{
			holds >>= 1;
			if(stats & 0x01)
			{				
				if(hold_dly[k] <= BTN_HOLD_TIME)
					hold_dly[k]++;
				if(hold_dly[k] == BTN_HOLD_TIME)
					holds |= 0x80;
			}
			else
				hold_dly[k] = 0;
			stats >>= 1;
		}
		ui.holds |= holds;
				
		tick_blink_div--;
		if(!tick_blink_div)
		{
			tick_blink_div = 5;
			led_blink = !led_blink;
		}

		if(timeout_led)
			timeout_led--;

		tick_1s_div--;
		if(!tick_1s_div)
		{
			tick_1s_div = 100;
			// 1s tick

			if(timeout_sleep)
				timeout_sleep--;

			if(uvlo_timeout)
				uvlo_timeout--;
		}
	}

	// generate LED state
	if(led_state == LED_RED)
		led_set(LED_RED);
	else if(led_state == LED_GREEN)
		led_set(LED_GREEN);
	else if(led_state == LED_GREEN_BLINK && led_blink)
		led_set(LED_GREEN);
	else if(led_state == LED_RED_BLINK && led_blink)
		led_set(LED_RED);
	else if(led_state == LED_RG_BLINK && led_blink)
		led_set(LED_RED);
	else if(led_state == LED_RG_BLINK && !led_blink)
		led_set(LED_GREEN);
	else if(led_state == LED_ORANGE && tick_10ms_div > 8)
		led_set(LED_GREEN);
	else if(led_state == LED_ORANGE)
		led_set(LED_RED);
	else
		led_set(LED_IDLE);

}


// init system timer
void sys_timer_init()
{
	// system tick
	TCCR1A = (0<<WGM10);
	TCCR1B = (1<<WGM12)|(1<<CS00);
	OCR1A = SYS_TICK_DIV;
	TIMSK1 = (1<<OCIE1A);

	sys_flags = 0;
	timeout_led = 0;
	timeout_sleep = 0;
}

//----------------------------------------------------------------------------------
// Other stuff
//----------------------------------------------------------------------------------

// send 0/1
void serial_tx_bool(uint8_t state)
{
	if(state)
		serial_tx_cstr(PSTR("1\n"));
	else
		serial_tx_cstr(PSTR("0\n"));
}

// crc16 CCITT somewhere from internet
//   set input crc to 0xFFFFu before first call
//   call several times for separate parts of data if needed
uint16_t crc16(uint16_t crc, uint8_t* data_p, uint16_t length){

	//u16 crc = 0xFFFF;
	while(length--){
		uint16_t x = crc >> 8 ^ *data_p++;
		x ^= x>>4;
		crc = (crc << 8) ^ (x << 12) ^ (x << 5) ^ (x);
	}
	return(crc);
}




//----------------------------------------------------------------------------------
// EEPROM
//----------------------------------------------------------------------------------

#define EEPROM_CAL_ADDR 0 // calibration data offset

// try to load calibration data
uint8_t ee_load_cal(TSetup *data)
{	
	// get record
	TSetup buf;
	uint8_t *addr = (uint8_t*)EEPROM_CAL_ADDR;
	eeprom_read_block((void*)&buf, addr, sizeof(TSetup));
	uint16_t crc = crc16(0xFFFFu, (uint8_t*)&buf, sizeof(TSetup));
	uint16_t ee_crc;
	eeprom_read_block((void*)&ee_crc, addr+sizeof(TSetup), sizeof(uint16_t));
	if(crc != ee_crc)
		return(1);
	memcpy((void*)data, (void*)&buf, sizeof(TSetup));
	return(0);
}

// save calibration data
uint8_t ee_save_cal(TSetup *data)
{	
	uint8_t *addr = (uint8_t*)EEPROM_CAL_ADDR;
	eeprom_write_block((void*)data,addr,sizeof(TSetup));
	uint16_t crc = crc16(0xFFFFu, (uint8_t*)data, sizeof(TSetup));
	eeprom_write_block((void*)&crc,addr+sizeof(TSetup),sizeof(uint16_t));
	return(0);
}


//----------------------------------------------------------------------------------
// MAIN
//----------------------------------------------------------------------------------
int main(void)
{
	// disable WDT if enabled (sometimes it fucks up ...)
	uint8_t rst_flag = MCUSR;
	MCUSR = 0;
	wdt_disable();

	// disable all ports
	DDRB = 0x00;
	DDRC = 0x00;
	DDRD = 0x00;
	
	if(bit_is_set(rst_flag,BORF))
	{
		// brown-out reset
		_delay_ms(200);
	}
		
	led_state = LED_IDLE;
	
	// init ADC
	adc_init();

	// set Vmon alert
	adc_set_vmon_alert(VMON_MIN_ALERT);

	// init PWM controller
	pwm_init();
		
	// serial input init
	serial_init();

	// enable power
	pwm_enable();

	// system timer
	ctrl_init();
	led_init();
	sys_timer_init();
	
	// enable ISR
	sei();

	// motor calibration
	TMotor mot;
	mot.speed = 0.0;
	mot.speed_act = 0.0;
	mot.speed_mem = 0.0;
	mot.acc = 500.0;
	mot.speed_lim = 270.0;
	mot.amp_min = 90.0;
	mot.amp_max = 255.0;
	mot.speed_min = 60.0;
	mot.speed_max = 180.0;
	
	// default system setup
	TSetup setup;
	setup.sleep_timout = SLEEP_TIMEOUT;
	setup.mot_speed_lim = mot.speed_lim;

	// try load EEPROM setup
	if(!ee_load_cal(&setup))
	{
		// CRC passed
		mot.acc = setup.mot_acc;
		mot.speed_lim = setup.mot_speed_lim;
	}
			
	// update motor cal data
	mot_update_cal(&mot);

	// reset sleep timeout
	set_sleep_timeout(setup.sleep_timout);

	// wait for power stage charge
	for(uint16_t k = 0; k < 2000; )
		k += adc_conv_done();
	
	while(1)
	{

		char str[64]; // response buffer
		char cmd[RX_BUF_SZ]; // local command buffer
		char *par;
		uint8_t sleep_reset = 0;
		if(serial_decode(cmd,&par))
		{
			// --- command detected ---
			set_led_timeout(LED_BLINK_TIMEOUT);

			// reset sleep timeout flag
			sleep_reset = 1;
						
			// parse command				    
			if(!strcmp_P(cmd,PSTR("SYST:VMON?")))
			{
				// return system voltage
				float vmon = adc_get_vmon();
				snprintf_P(str, sizeof(str), PSTR("%.2f\n"), vmon);
				serial_tx_str(str);
			}			
			else if(!strcmp_P(cmd,PSTR("SYST:TEMP?")))
			{
				// return system temperature
				float temp = adc_get_temp();
				snprintf_P(str, sizeof(str), PSTR("%.0f\n"), temp);
				serial_tx_str(str);
			}
			else if(!strcmp_P(cmd,PSTR("SPEED")))
			{
				// set speed (signed rpm value)
				if(!par)
				{
					serial_error(SCPI_ERR_tooFewParameters,PSTR("SPEED <speed> - missing speed value!"),SCPI_ERR_STORE|SCPI_ERR_PSTR);
					goto SCPI_error;
				}
				mot.speed = atof(par);
			}
			else if(!strcmp_P(cmd,PSTR("SPEED?")))
			{
				// get current speed (signed rpm value)
				snprintf_P(str, sizeof(str), PSTR("%.1f\n"), mot.speed_act);
				serial_tx_str(str);
			}
			else if(!strcmp_P(cmd,PSTR("SPEED:SET?")))
			{
				// get target speed (signed rpm value)
				snprintf_P(str, sizeof(str), PSTR("%.1f\n"), mot.speed_mem);
				serial_tx_str(str);
			}
			else if(!strcmp_P(cmd,PSTR("SPEED:LIMIT")))
			{
				// set speed limit [rpm]
				if(!par)
				{
					serial_error(SCPI_ERR_tooFewParameters,PSTR("MOT:ACC <acc> - missing acceleration value [rpm/s]!"),SCPI_ERR_STORE|SCPI_ERR_PSTR);
					goto SCPI_error;
				}
				float lim = atof(par);
				if(lim < 1.0 || lim > 500.0)
				{
					serial_error(SCPI_ERR_wrongParamType,PSTR("SPEED:LIMIT <limit> - allowed range is 1 to 500 rpm!"),SCPI_ERR_STORE|SCPI_ERR_PSTR);
					goto SCPI_error;
				}
				mot.speed_lim = lim;
			}
			else if(!strcmp_P(cmd,PSTR("SPEED:LIMIT?")))
			{
				// get speed limit [rpm]
				snprintf_P(str, sizeof(str), PSTR("%.1f\n"), mot.speed_lim);
				serial_tx_str(str);
			}
			else if(!strcmp_P(cmd,PSTR("STOP")))
			{
				// stop
				mot.speed = 0.0;
			}
			else if(!strcmp_P(cmd,PSTR("START")))
			{
				// start with last known speed
				mot.speed = mot.speed_mem;
			}
			else if(!strcmp_P(cmd,PSTR("DIR")))
			{
				// switch direction (or restart from stop)
				if(!par)
				{
					serial_error(SCPI_ERR_tooFewParameters,PSTR("DIR <direction> - missing direction value!"),SCPI_ERR_STORE|SCPI_ERR_PSTR);
					goto SCPI_error;
				}
				if(strcmp_P(par,PSTR("CW")) == 0)
					mot.speed = fabs(mot.speed_mem);
				else if(strcmp_P(par,PSTR("CCW")) == 0)
					mot.speed = -fabs(mot.speed_mem);
				else
				{
					serial_error(SCPI_ERR_wrongParamType,PSTR("DIR <direction> - invalid direction value! Use CW or CCW."),SCPI_ERR_STORE|SCPI_ERR_PSTR);
					goto SCPI_error;
				}
			}
			else if(!strcmp_P(cmd,PSTR("SLEEP")))
			{
				// goto sleep now
				sleep_reset = 0;
				set_sleep_timeout(SLEEP_TIMEOUT_NOW);
			}
			else if(!strcmp_P(cmd,PSTR("SLEEP:TIMEOUT")))
			{
				// set sleep timeout [s]
				if(!par)
				{
					serial_error(SCPI_ERR_tooFewParameters,PSTR("SLEEP:TIMEOUT <timeout> - missing timeout value [s]!"),SCPI_ERR_STORE|SCPI_ERR_PSTR);
					goto SCPI_error;
				}
				setup.sleep_timout = atoi(par);
			}
			else if(!strcmp_P(cmd,PSTR("SLEEP:TIMEOUT?")))
			{
				// get sleep timeout [s]
				snprintf_P(str, sizeof(str), PSTR("%u\n"), setup.sleep_timout);
				serial_tx_str(str);
			}
			else if(!strcmp_P(cmd,PSTR("MOT:ACC")))
			{
				// set motor acceleration [rpm/s]
				if(!par)
				{
					serial_error(SCPI_ERR_tooFewParameters,PSTR("MOT:ACC <acc> - missing acceleration value [rpm/s]!"),SCPI_ERR_STORE|SCPI_ERR_PSTR);
					goto SCPI_error;
				}
				float acc = atof(par);
				if(acc < 100.0 || acc > 2000.0)
				{
					serial_error(SCPI_ERR_wrongParamType,PSTR("MOT:ACC <acc> - allowed range is 100 to 2000 rpm/s!"),SCPI_ERR_STORE|SCPI_ERR_PSTR);
					goto SCPI_error;
				}
				mot.acc = acc;
			}
			else if(!strcmp_P(cmd,PSTR("MOT:ACC?")))
			{
				// get motor acceleration [rpm/s]
				snprintf_P(str, sizeof(str), PSTR("%.1f\n"), mot.acc);
				serial_tx_str(str);
			}
			else if(!strcmp_P(cmd,PSTR("SYST:EESAVE")))
			{
				// store current setup to EEPROM
				setup.mot_acc = mot.acc;
				setup.mot_speed_lim = mot.speed_lim;
				ee_save_cal(&setup);
			}
			else if(!strcmp_P(cmd,PSTR("*OPC?")))
			{
				// *OPC? - returns 1 when HW is set
				serial_tx_cstr(PSTR("1\n"));
			}
			else if(!strcmp_P(cmd,PSTR("*IDN?")))
			{
				// "*IDN?" to return IDN string
				serial_tx_cstr(PSTR("Merkur Motor controller by Stanislav Maslan V1.0, " __DATE__ "\n"));
			}			
			else if(!strcmp_P(cmd,PSTR("SYST:ERR?")))
			{
				// SYST:ERR? - return last error
				serial_error(SCPI_ERR_undefinedHeader,NULL,SCPI_ERR_SEND);
			}
			/*else if(!strcmp_P(cmd,PSTR("SYST:BOOT")))
			{
				// SYST:BOOT <password> - initiates bootloader

				// send ACK/NACK
				if(par && !strcmp_P(par,PSTR("17IND10")))
				{
					// send ACK
					serial_tx_cstr(PSTR("1\n"));

					// get extended fuse bits
					uint8_t fuex = boot_lock_fuse_bits_get(GET_EXTENDED_FUSE_BITS);

					// extract bootsize index (FUSE_BOOTSZ1:FUSE_BOOTSZ0)
					fuex = !!(fuex&(~FUSE_BOOTSZ0)) + (!!(fuex&(~FUSE_BOOTSZ1))<<1);

					// calculae bootloader start address in [Bytes]
					uint16_t addr = FLASHEND + 1 - (1024ul<<(3 - fuex));
								
					// jump to boot section
					cli();
					boot_start(addr);
				}
				else
					serial_tx_cstr(PSTR("0\n"));
			}*/
			else if(!strcmp_P(cmd,PSTR("CONNECTED")))
			{
				// fake command produced by BT module - ignore
			}
			else
			{
				// invalid
				serial_error(SCPI_ERR_undefinedHeader,cmd,SCPI_ERR_STORE|SCPI_ERR_STR);
				goto SCPI_error;
			}

			// jump site when error occurred
			SCPI_error:;
				    
		}



		// process ADC data
		adc_conv_done();
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

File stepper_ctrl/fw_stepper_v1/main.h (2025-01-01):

/*
 * Simple stepper motor controller. More details here:
 * https://github.com/smaslan/Merkur-Motor
 *
 * (c) 2024-2025, Stanislav Maslan, s.maslan@seznam.cz
 * V1.0, 2025-01-01
 *
 * The code and all its part are distributed under MIT license
 * https://opensource.org/licenses/MIT.
 */ 

#ifndef MAIN_H
#define MAIN_H

// general macros
#define sbi(port,pin) {(port)|=(1<<pin);}
#define cbi(port,pin) {(port)&=~(1<<pin);}
#define min(a,b) ((a<b)?(a):(b))
#define max(a,b) ((a>b)?(a):(b))
#define bcopy(dreg,dpin,srreg,srpin) if(bit_is_set((srreg),(srpin))){sbi(dreg,dpin);}else{cbi(dreg,dpin);}
#define bcopy_v(dreg,dpin,srreg,srpin) if((srreg)&(1<<srpin)){sbi(dreg,dpin);}else{cbi(dreg,dpin);}
#define low(x) ((x) & 0xFFu)
#define high(x) (((x)>>8) & 0xFFu)

// PWR control (active high)
#define PWR_port PORTD
#define PWR_ddr DDRD
#define PWR PD3

// control switches (active low)
#define SW_A_port PORTB
#define SW_A_ddr DDRB
#define SW_A_pin PINB
#define SW_A PB0
#define SW_B_port PORTD
#define SW_B_ddr DDRD
#define SW_B_pin PIND
#define SW_B PD7
#define SW_START_port PORTB
#define SW_START_ddr DDRB
#define SW_START_pin PINB
#define SW_START PB2
#define SW_STOP_port PORTB
#define SW_STOP_ddr DDRB
#define SW_STOP_pin PINB
#define SW_STOP PB1
#define SW_START_PCIE PCIE0
#define SW_START_PCMSK_REG PCMSK0
#define SW_START_PCMSK (1<<SW_START)
#define SW_START_ISR PCINT0_vect

// encoder (active low)
#define ENC_port PORTC
#define ENC_ddr DDRC
#define ENC_pin PINC
#define ENC_phy PC2
#define ENA_phy PC4
#define ENB_phy PC3
#define ENC 3
#define ENA 4
#define ENB 5
#define ENC_PCIE PCIE1
#define ENC_PCMSK_REG PCMSK1
#define ENC_PCMSK (1<<ENC_phy)
#define ENC_ISR PCINT1_vect

// BT state (active high)
#define BT_STATE_port PORTC
#define BT_STATE_ddr DDRC
#define BT_STATE_pin PINC
#define BT_STATE PC5

// serial port
#define UART_port PORTD
#define UART_ddr DDRD
#define UART_RXD PD0
#define UART_TXD PD1

// state LED (dual color)
#define LED_port PORTC
#define LED_ddr DDRC
#define LED_A PC1
#define LED_C PC0

// pulse outputs
#define PWM_port PORTD
#define PWM_ddr DDRD
#define PWM_L1 PD6
#define PWM_L2 PD5

// analogue inputs
#define ADC_VMON_MUX 0x07
#define ADC_TEMP_MUX 0x08
// ADC averaging
#define ADC_AVG 32 /* max 10bit*64 to scale to full 16bit */

// ADC data and stuff
typedef struct{
	volatile uint16_t a_vmon;
	volatile uint16_t a_temp;
	uint16_t vmon_alert;
}TADC;

// state LED modes
#define LED_IDLE 0
#define LED_RED 1
#define LED_GREEN 2
#define LED_RED_BLINK 3
#define LED_GREEN_BLINK 4
#define LED_RG_BLINK 5
#define LED_ORANGE 6

// system tick flag
#define SYS_10MS_TICK 0

// controls struct
typedef struct{
	volatile uint8_t downs;
	volatile uint8_t states;
	volatile uint8_t holds;
	volatile int8_t enc_delta;
	volatile uint8_t flags;
}TUI;

// encoder state changed (must not collide with button/encoder flags)
#define UI_ENC_CHANGE 6

// system setup to store to EEPROM
typedef struct{
	uint16_t sleep_timout;
	float mot_acc;
	float mot_speed_lim;
}TSetup;

// motor control
typedef struct{
	float speed;
	float speed_mem;
	float acc;
	float speed_act;
	float speed_lim;
	float speed_min;
	float speed_max;
	float amp_min;
	float amp_max;
	float amp_coef;
}TMotor;

// main system timer
#define SYS_TICK 0.001
#define SYS_TICK_DIV ((uint16_t)(F_CPU*SYS_TICK - 1))

// button hold off time [10ms]
#define BTN_HOLD_TIME 70

// battery undervolt alert voltage [V]
#define VMON_MIN_ALERT 4.2

// LED blink timeout for serial command [10ms]
#define LED_BLINK_TIMEOUT 25

// default sleep timeout [s]
#define SLEEP_TIMEOUT 60

// uvlo detection timeout [s]
#define UVLO_DET_TIMEOUT 5

// undervolt sleep timeout [s]
#define SLEEP_TIMEOUT_UVLO 3

// immediate sleep timeout [s]
#define SLEEP_TIMEOUT_NOW 0

// power stage voltage to allow sleep [V]
#define VMON_POWER_IDLE 2.0


#endif
